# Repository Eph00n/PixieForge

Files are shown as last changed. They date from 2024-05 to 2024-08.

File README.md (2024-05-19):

# PixieForge
An ultra-portable, foldable 3D Printer.  

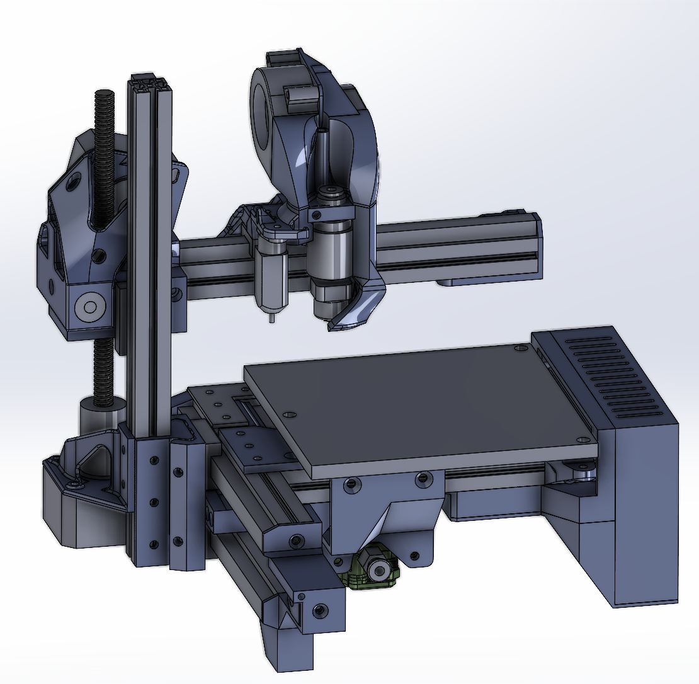
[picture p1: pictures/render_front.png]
  

## What is it?
The PixieForge is a small 3D printer that folds up when not in use, making it small enough to fit inside a filament box.  
This project started as a simple extension of [eponra's flatpack 3D printer](https://github.com/eponra/flatpack/), but quickly turned into a complete redesign with a focus on ease of use and reliability.

The foldable design makes it suitable for anyone who either doesn't have the space for a printer or wants to use it on the move.  

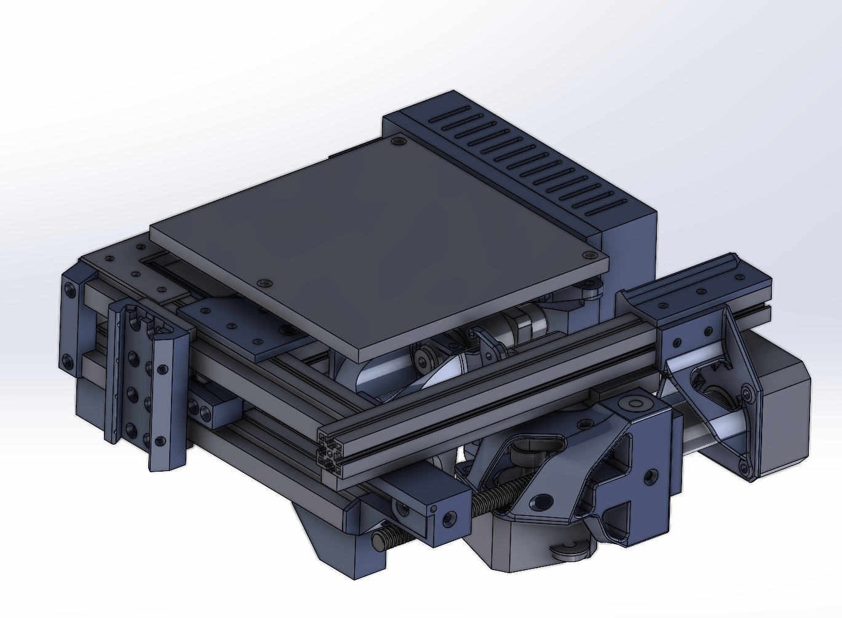
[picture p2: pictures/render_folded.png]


## Technical specifications
- Print volume: 120x120x120mm
- Machine size folded: 205x206x79mm
- Max. Bed temperature: 120°C (using a Voron0 bed)
- Max. Hotend temperature: 300°C (using a TriangleLabs CHC mini)
- Extruder system: Bowden (using a modified Sherpa Micro)
- Power consumption: not yet measured. Approx 120W peak and much less during operation
- Power input: 24V, 5.5mm barrel plug (150W power supply recommended, but could run on battery)
- Bed levelling: BLTouch/Automatic
- Controller: BTT SKR pico + Raspberry Pi Zero 2W (running on Klipper)

## Design choices
**Ease of use and accessibility**  
Wherever possible, the PixieForge uses parts that are compatible with other open source projects, making sourcing much easier.  
Most of the printed parts don't need supports and the build process is fairly straightforward (although a little finicky).  
Also, the price for a complete machine should be under 350$.

**Reliability**  
The PixieForge is designed to make as few compromises as possible (obviously some had to be made).  
It is fully capable of printing technical materials, uses automatic bed leveling, runs Klipper and so on...  
As the hotend assembly is modular, it can be easily adapted to work with other hotends.  
It currently uses the TriangleLabs CHC Mini, which has a quick-change heatbreak/nozzle assembly (using M6 nozzles).

**Compromises**  
This printer uses fixed-bed cantilever kinematics (i.e. the bed is fixed and the whole Z-tower moves along the X-axis).  
These kinematics aren't the best choice in terms of rigidity, but they do allow the printer to fold up and free up space under the bed.  
For such a small printer this won't be a problem, just don't expect to break any speed records.  

Currently there is no display on the machine.  
It is fully controlled via WiFi and the end device of your choice. Hopefully this will change in a future release.  

## Next Steps  
- Finishing the Github Repo, finalizing the BOM, etc.

**short-term**
- Stress-testing the printer and using it.
- Evaluating speed and power draw.
- Creating a building-manual.
- Creating nicer looking CAD files for aftermarket parts.  
- Adding all fasteners to the CAD assembly.  

**long-term**
- Redesigning the electronics-bay and adding the option for a display.
- Adding support for more hotends.
- Further reducing cost.

## Contributions
I'd like to thank everyone in the flatpack group for their support during the development of this project! Especially eponra for creating an awesome 3D printer.

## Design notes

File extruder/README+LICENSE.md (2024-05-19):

This extruder is based on the [awesome sherpa micro](https://github.com/Annex-Engineering/Sherpa_Micro-Extruder/tree/main) created by AnnexEngineering.  
As a fork of the original sherpa micro, this extruder is subject to the license agreement of annex engineering, which you may find here:  
https://github.com/Annex-Engineering/ANNEX-Engineering-License-Agreement

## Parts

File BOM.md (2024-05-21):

# Bill of materials

### List of printed parts:  
https://docs.google.com/spreadsheets/d/e/2PACX-1vTd6-dzrgt3s1AHt093iQwWVIKAQ9prgNHli51OY2EO9juYl3RYXV6nNz6ilWRrEIvzmtFYT-dx4qe8/pubhtml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  

### List of aftermarket items:  
https://docs.google.com/spreadsheets/d/e/2PACX-1vTREqxtrdG4AC5djyYq19owuAr4M0oSJCOitgPbOmvA0bEyIfAJhsUJKBzVDEeSJPbEEB_p5hLRu8nv/pubhtml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

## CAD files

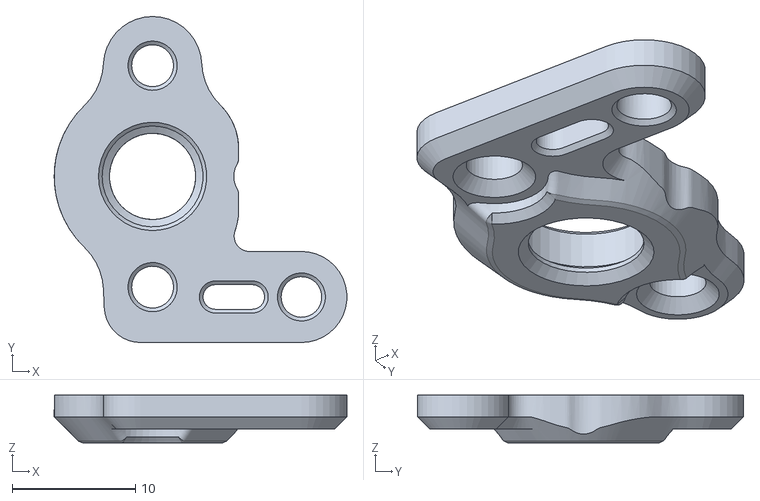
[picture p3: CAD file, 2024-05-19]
extruder/housing_front_pixie.STL
23.8 x 26.5 x 3.90

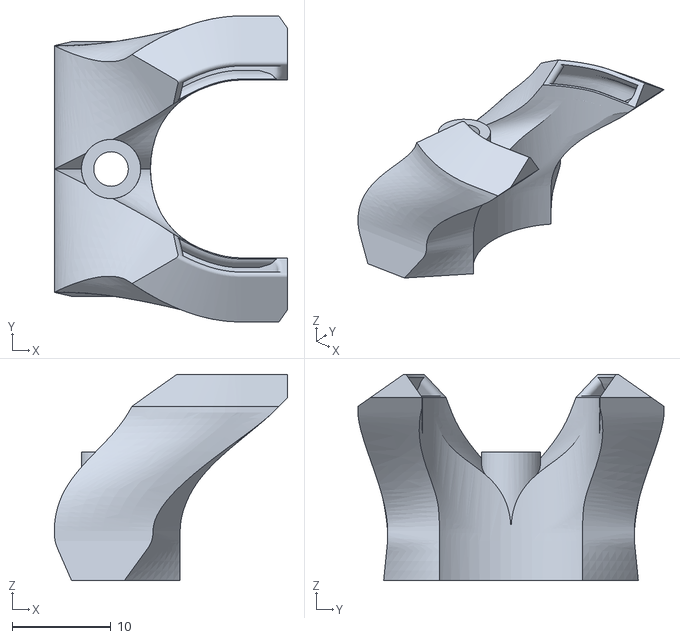
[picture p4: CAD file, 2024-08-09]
printer/stl/cooling_nozzle_4.STL
23.6 x 31.0 x 20.9

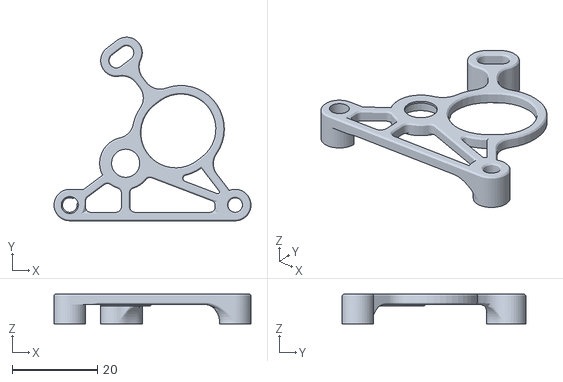
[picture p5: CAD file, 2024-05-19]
extruder/housing_rear_pixie.STL
46.2 x 43.1 x 7.00

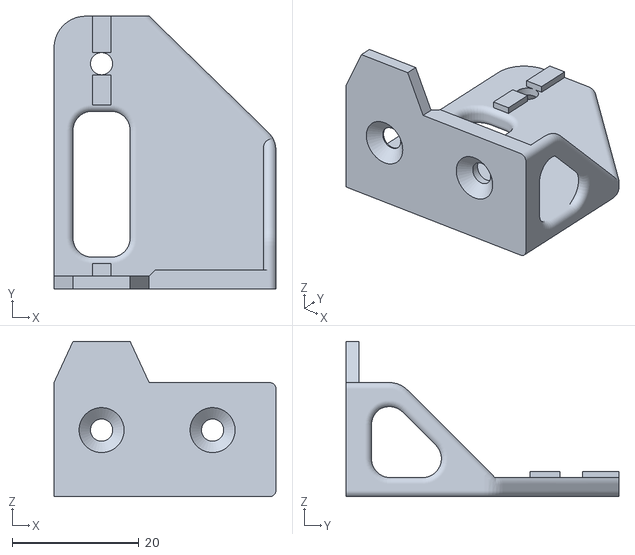
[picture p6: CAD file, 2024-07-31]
printer/stl/y_idler_mount_2.STL
35.0 x 43.0 x 24.5

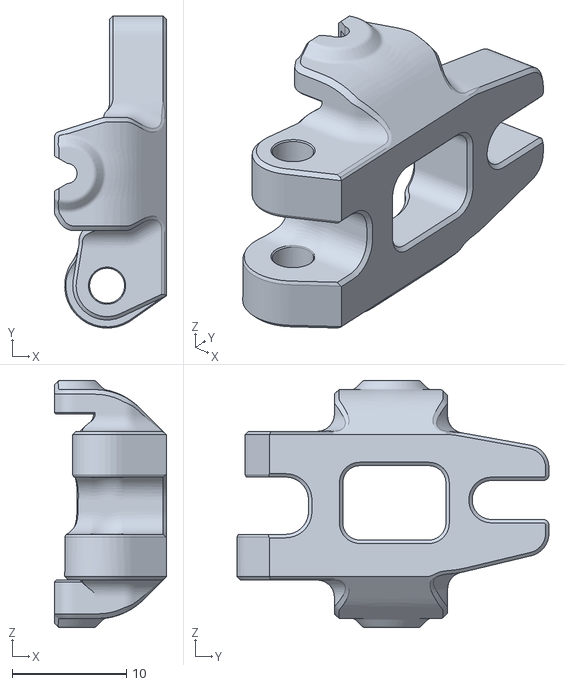
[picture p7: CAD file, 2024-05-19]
extruder/idler_arm_pixie.STL
9.80 x 27.3 x 21.6

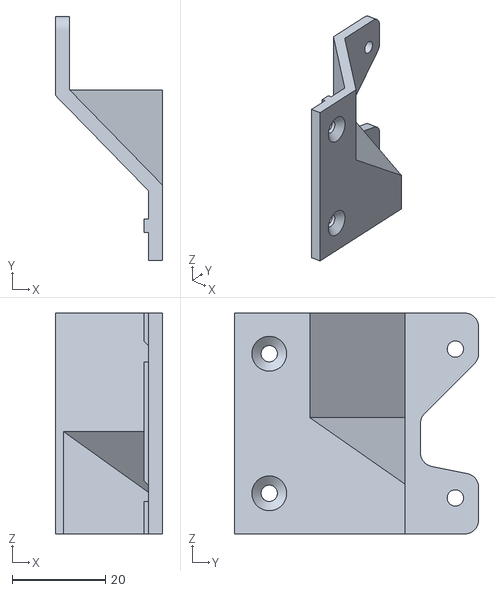
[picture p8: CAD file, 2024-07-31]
printer/stl/extruder_mount_2.STL
23.0 x 52.5 x 47.5

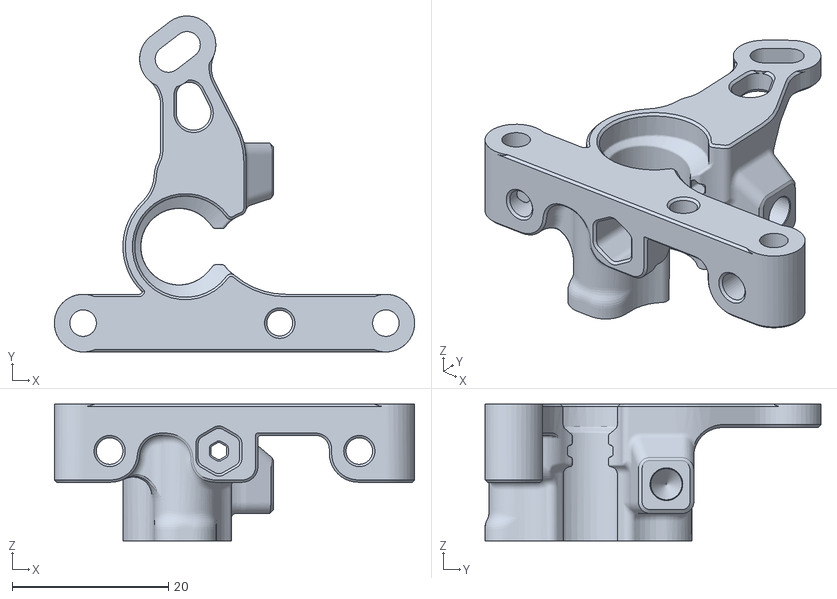
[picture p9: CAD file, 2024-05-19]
extruder/housing_core_pixie.STL
46.2 x 43.1 x 17.5

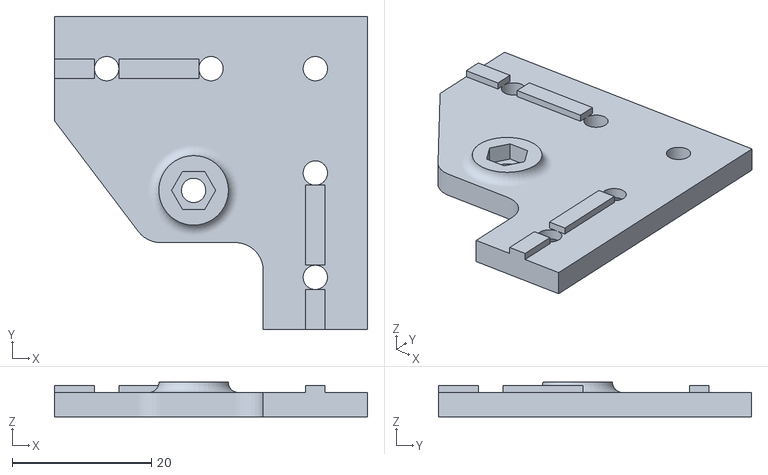
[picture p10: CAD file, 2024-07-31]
printer/stl/build_plate_mount_B_2.STL
45.0 x 45.0 x 5.00

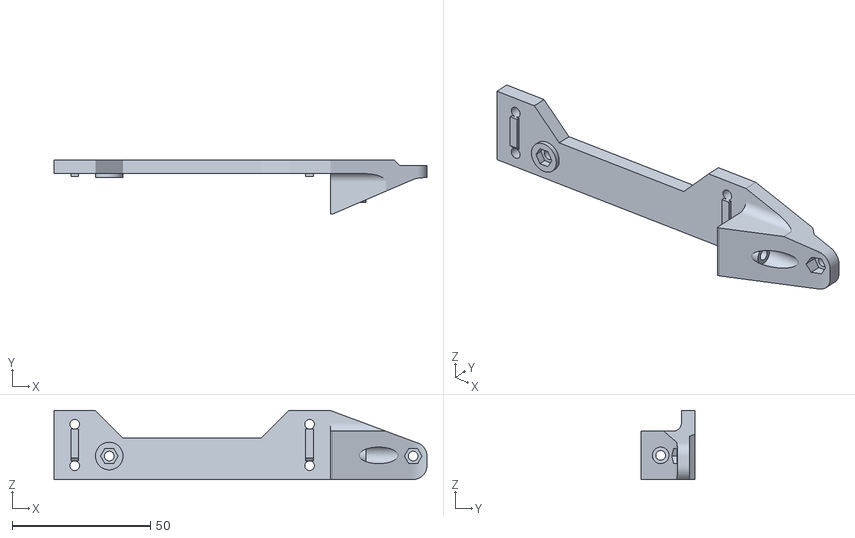
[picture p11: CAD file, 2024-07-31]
printer/stl/build_plate_mount_A_2.STL
135.0 x 19.7 x 25.0

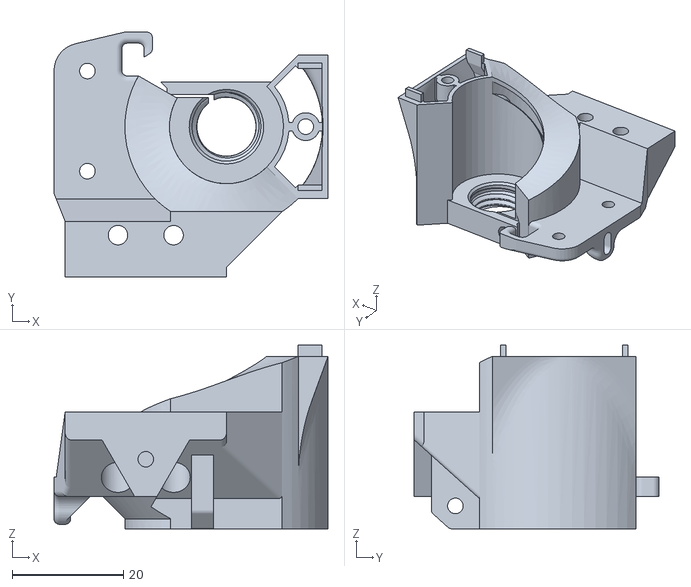
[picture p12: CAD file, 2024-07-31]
printer/stl/integrated_duct_3.STL
49.2 x 44.0 x 33.0

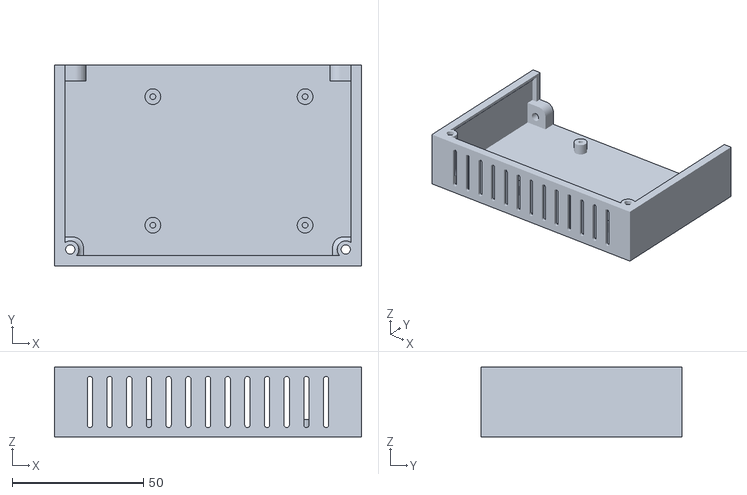
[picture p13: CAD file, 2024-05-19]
printer/stl/pico_holder_1.STL
117.0 x 76.5 x 26.5

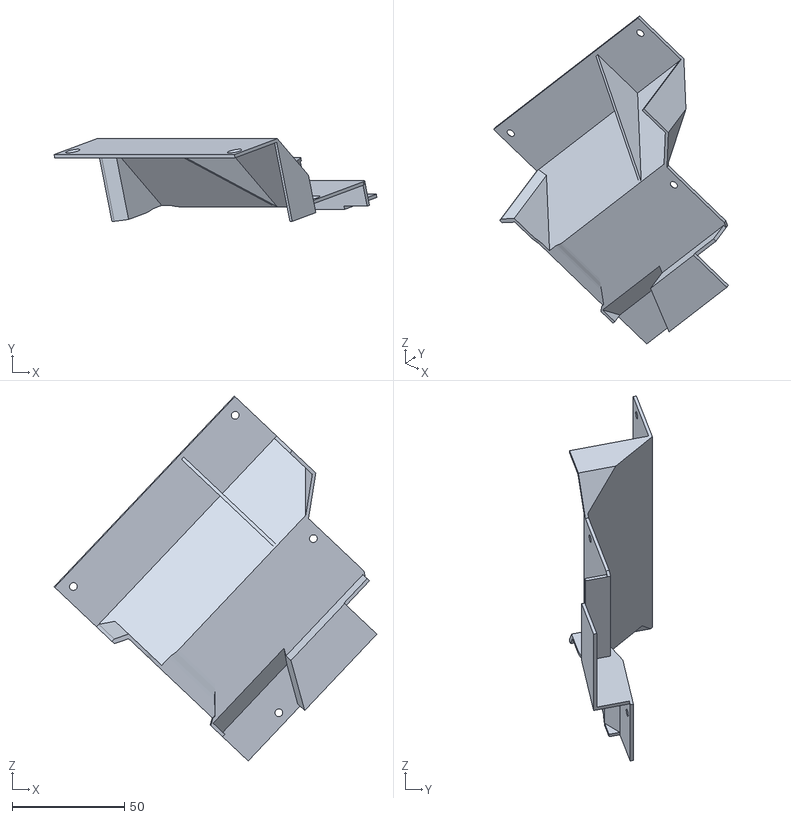
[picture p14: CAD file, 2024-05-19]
printer/stl/e_bay_cover_1.STL
143.9 x 36.9 x 162.7

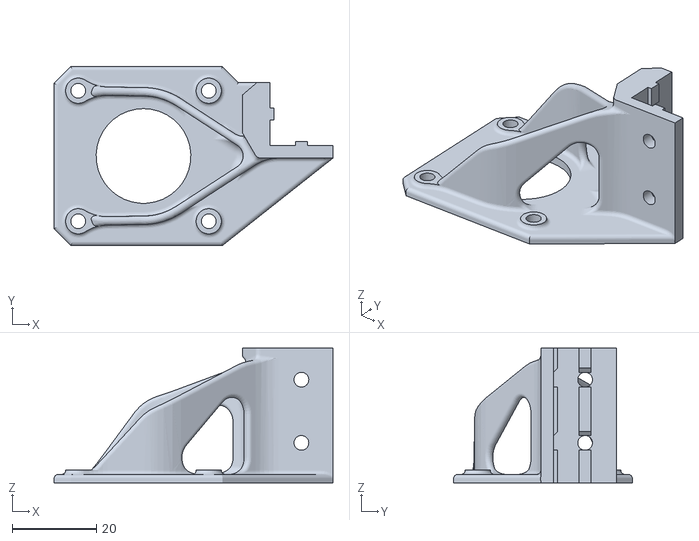
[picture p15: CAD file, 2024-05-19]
printer/stl/z_motor_mount_3.STL
66.2 x 42.5 x 32.0

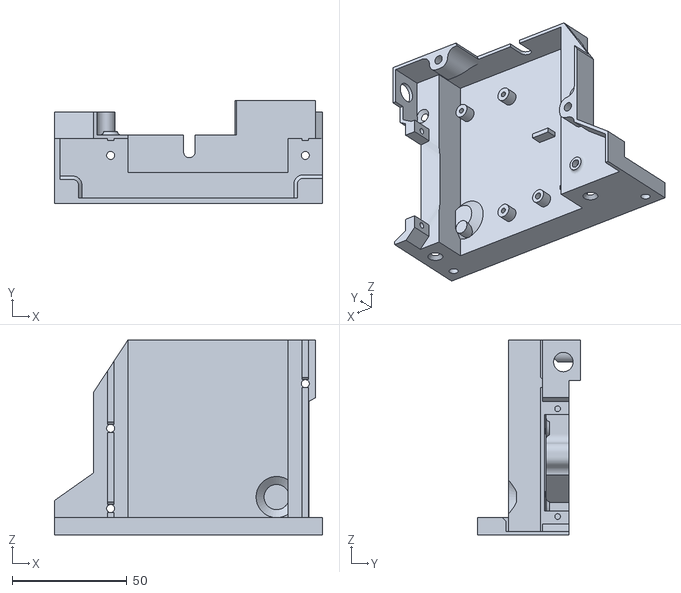
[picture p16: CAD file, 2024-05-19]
printer/stl/e_bay_2.STL
117.0 x 45.0 x 85.0

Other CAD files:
printer/stl/x_idler_holder_1.STL
printer/stl/y_idler_holder_1.STL
printer/stl/x_belt_mount_1.STL
printer/stl/joint_female_2.STL
printer/stl/belt_screw_block_1.STL
printer/stl/fan_mount_1.STL
printer/stl/foot_1.STL
printer/stl/joint_male_2.STL
printer/stl/x_bumper_1.STL
printer/stl/x_idler_mount_2.STL
printer/stl/x_motor_mount_2.STL
printer/stl/y_belt_mount_1.STL
printer/stl/y_motor_mount_2.STL
printer/stl/yz_crossplate_1.STL

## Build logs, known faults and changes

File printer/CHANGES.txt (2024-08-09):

intermittent changes:
-cooling_nozzle_4: increased clearance between cooling nozzle and print surface

01.08.2024 release r2
-general: added aluminium braceplates on z tower to improve torsion resistance during x moves
-build_plate_mount_A_2: changed print direction and slightly modified geometry to be printable without supports
-build_plate_mount_B_2: added clearance for wire bulge on keenovo silicone heatmats
-cooling_nozzle_3: smoothed airflow path and simplified CAD-model
-extruder_mount_2: changed clearance between extruder motor and electronics compartment
-integrated_duct_3: smoothed airflow path to part cooling nozzle
-y_idler_mount_2: replaced socket head screw with countersunk screw to add more clearance between the part and the build plate

19.05.2024 initial release r1
-belt_screw_block_1
-build_plate_mount_A_1
-build_plate_mount_B_1
-cooling_nozzle_2
-e_bay_2
-e_bay_cover_1
-extruder_mount_1
-fan_mount_1
-foot_1
-integrated_duct_2
-joint_female_2
-joint_male_2
-pico_holder_1
-x_belt_mount_1
-x_bumper_1
-x_idler_holder_1
-x_idler_mount_2
-x_motor_mount_2
-y_belt_mount_1
-y_idler_holder_1
-y_idler_mount_1
-y_motor_mount_2
-yz_crossplate_1
-z_motor_mount_3

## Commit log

2024-07-31 superseded in release r2
    [build_plate_mount_A_1.STL]
2024-08-09 cooling_nozzle_3 superseded by cooling_nozzle_4
    increased the clearance between cooling nozzle and print surface by 1mm
    [cooling_nozzle_3.STL]
